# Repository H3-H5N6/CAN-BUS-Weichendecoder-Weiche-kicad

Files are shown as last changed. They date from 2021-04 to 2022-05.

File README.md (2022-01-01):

# CAN-BUS Weichendecoder

## Serielle Console
Auf der seriellen Console kann man die Konfiguration einsehen und und die Modul-Id ändern.

Die Serielle Schnittstelle muss dazu auf 115200 gesetzt werden

## Konfigiratuion ansehen

Mit der Taste "p" wird die aktuelle Konfiguartion angezeigt. Beispiel:

```
==== CAN-Konfiguration ====
Version:       1
Status ID:     2
CAN ID: [0] => 811
CAN ID: [1] => 812
CAN ID: [2] => 813
CAN ID: [3] => 814
CAN ID: [4] => 815
CAN ID: [5] => 816
CAN ID: [6] => 817
CAN ID: [7] => 818
CAN ID: [8] => 819
CAN ID: [9] => 820
===========================
```

## Modul-Adresse ändern:

Mit der Eingabe &lt;i> + Nr + &lt;Return> kann die Modul-Adresse geändert werden.

```
Neue ID: 2
Setze neue Id: 2
```

Der Weichendecoder liefert regelmäßig seinen aktuellen Zustand

## Protocol

### IDs

* 100 Frames mit der Id 100 dient dem Verändern des Zustandes
* 200 Sendet den aktuellen Zustand des Decoders, wenn die im ersten Datafeld (u_int16) angegebene Moduladresse mit der des Moduls übereinstimmt. Der Status selbst wird mit der Id 300 gesendet

## CAN-Bus-RJ45-Steckerbelegung

Quelle: https://www.opendcc.de/info/can/can_connector.html

    CAN Pinbelegung auf RJ45
    RJ45 	
    Pin	Signal	    Beschreibung
    1 	CAN_H       Dominant High
    2 	CAN_L    	Dominant Low
    3 	CAN_GND     Ground
    4 	Reserved    Upgrade Path  // DCC A
    5 	Reserved    Upgrade Path  // DCC B
    6 	CAN_SHLD    CAN Shield, Optional
    7 	CAN_GND     Ground
    8 	CAN_V+ 	    Power, Optional

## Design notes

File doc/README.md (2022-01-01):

# Aktueller Stand (26.11.2021)

Kernstück des Ganzen sind die Weichendecoder für motorische Antriebe mit Impulssteuerung. Zum Einsatz sollen die Antriebe MP6 von MTB kommen. Diese werden mit kurzen Impulse gesteuert, indem der jeweilige Schalteingang kurz gegen Masse gezogen werden. Die Antriebe selbst werden mit 12V DC betrieben und haben auch gleich die Herzstückpolaristaion an Bord.

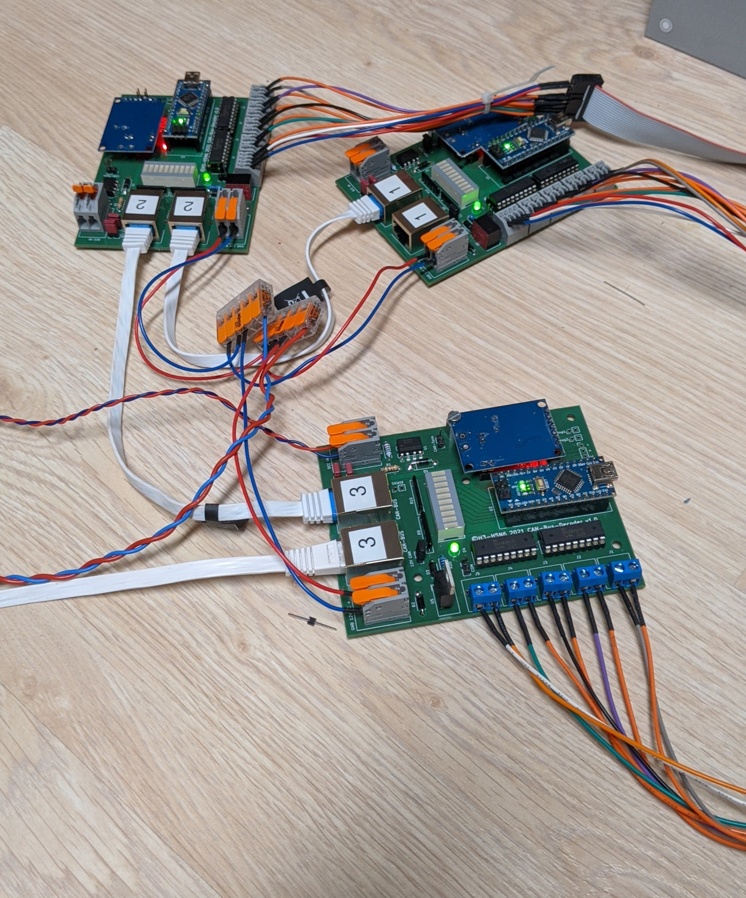
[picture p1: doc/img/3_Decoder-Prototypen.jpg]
Drei Weichendecoder


Geschaltet werden die Schaltausgänge 
* via CAN-BUS (und eigenem Protokoll)
* DCC
* oder für Testzwecke via USB-Console

CAN-BUS, DCC und auch 12V für die Versorgung der eigentlichen Elektronik erfolgt via einem RJ45-Netzwerkkabel.

Für Testzwecke gibt es auch eine kleine CAN-BUS-Zentrale  
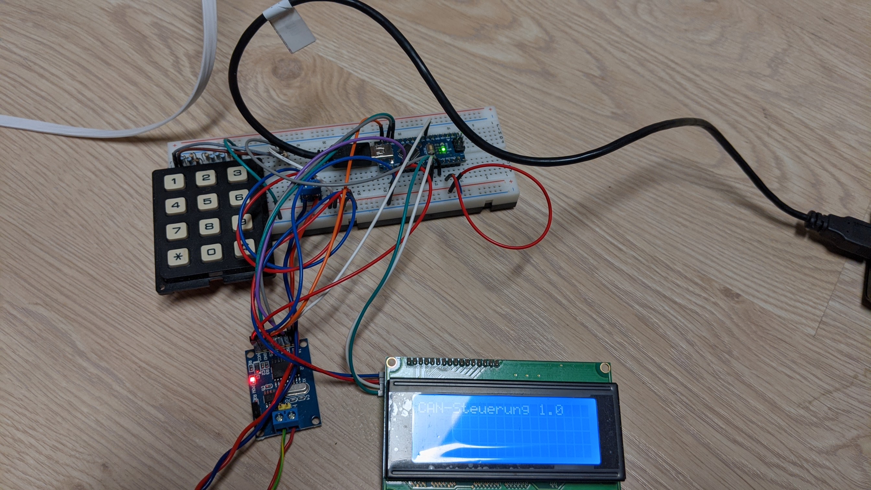
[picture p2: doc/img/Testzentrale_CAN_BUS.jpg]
CAN-Bus-Zentrale


Über die Eingabe von einer "Adresse" können die einzelnen Schaltausgänge geschaltet werden. Auch das Schalten von Weichenstraße ist möglich.

Später soll das Ganze durch ein Stellpult mit Schaltern (und LEDs zur Anzeige) ersetzt werden.

Natürlich kann man die Ausgänge auch mit einer gewöhnlichen DCC-Zentrale geschaltet werden. Hier als Beispiel kommt eine ECOS von ESU zu Einsatz, die auch ein Stellpult kennt.

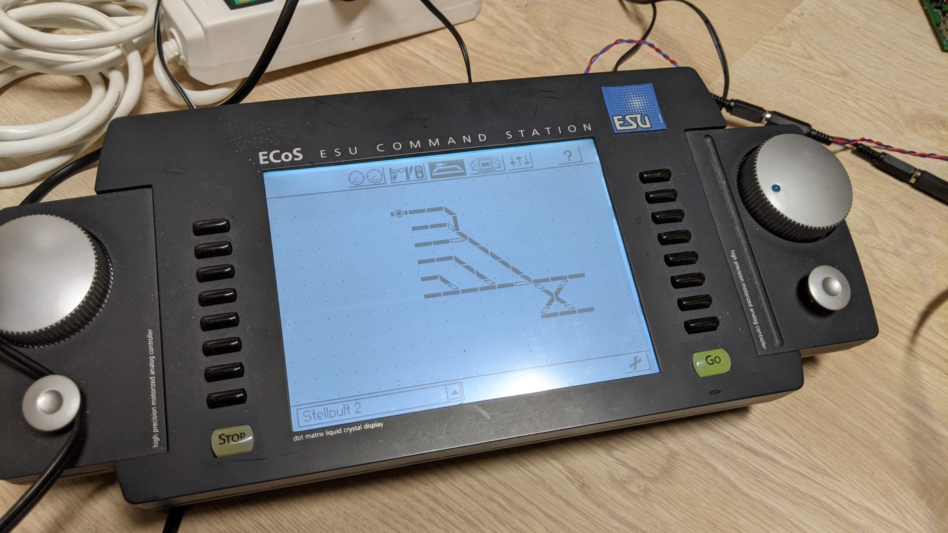
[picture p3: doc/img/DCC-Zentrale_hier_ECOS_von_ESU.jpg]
DCC-Zentrale


Da aktuell die Anlage ca 120km steht, wurde ein Modellbahn-Simulator gebaut. Die Weichenantriebe sind durch Bistabile Relais nachgebildet und die LED stellen die aktuelle Lage der Weichen wieder.

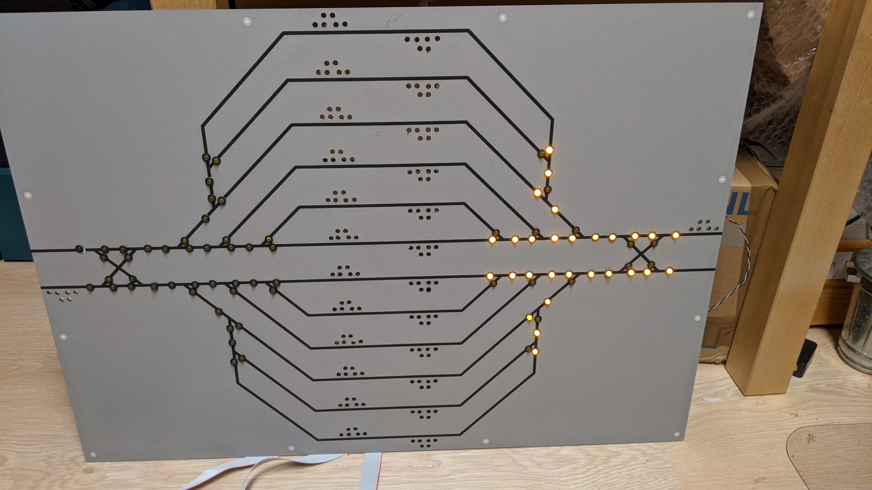
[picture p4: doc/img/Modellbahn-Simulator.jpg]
Modellbahn-Simulator

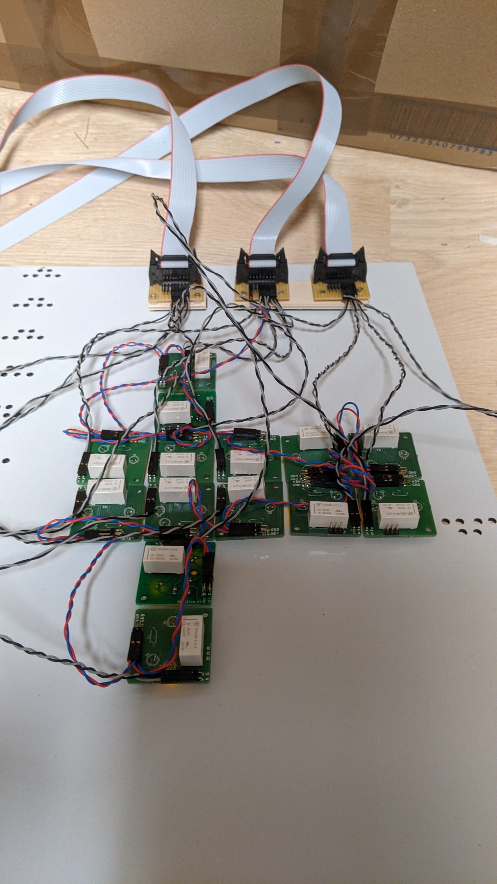
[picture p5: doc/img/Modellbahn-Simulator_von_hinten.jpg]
Modellbahn-Simulator Rückseite


# CAN-BUS-Frames

Die einzelnen Aktoren haben eine id im Wertebereich uint_16 (2byte)
## Aktor schalten

* Frame ID: 100
* data16: ID1 [, [ID2][, [ID3][, [ID4]]]]

Pro Frame können 4 Aktoren gleichzeit geschaltet werden

## Status der Aktoren

* Frame ID 300
* data16: ID des Aktor, Status des Aktors, unbenutz, ID des aktiven Aktors

### Bedeutung der Status

* OFF 0x00
* ON  0x01
* RUNNING 0x02
* BLOCKED_STATE 0x03
* UNKNOWN_STATE 0x04

Eine einfache Weiche besteht aus zwei Aktoren. Um den Status dieser Weiche zu erhalten, werden zwei Frames gesendet.

Hat der eine Aktor einen Status RUNNING, so hat der zweite Aktor einen Status von BLOCKED_STATE, da dieser aktuell nicht verändert werden kann. 

# Adapter Wannenstecker 2x3 zu Stiftleiste 1x6

## Adapter auf Lochrasterplatte, Ansicht von unten.


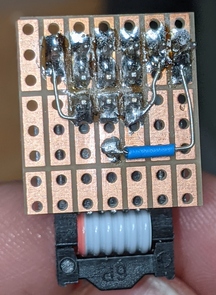
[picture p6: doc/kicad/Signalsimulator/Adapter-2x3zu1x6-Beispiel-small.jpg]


## Leiterplatte, Blick von oben auf die Bestückungsseite

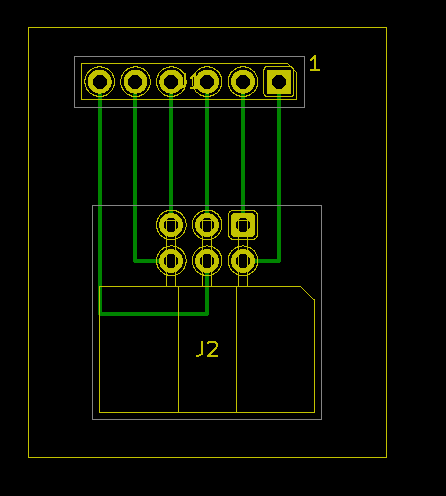
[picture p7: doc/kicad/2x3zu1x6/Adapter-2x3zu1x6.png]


## Belegung der 1x6-Stiftleiste, Blick von oben auf die Leiterplatte

6  |  5 |  4 |  3 | 2  | 1 
---|----|----|----|----|---
r1 | r2 | gr |  + | ge | w  

## Belegung des 2x3-Wannensteckers 

5  | 6  | 1  
---|----|----
r2 | r1 | w  
gr | +  | ge 
4  | 3  | 2

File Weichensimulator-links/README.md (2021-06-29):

# Weichensimulator links

## Releases
### v1.0

* Erster Entwurf

### v2.0

* Fix: Beschreibung der Platine auf der Oberseite, da Relais auf der Leiterseite plaziert wird 
* Change: 90°-Leiterbahnen durch 45° ersetzt

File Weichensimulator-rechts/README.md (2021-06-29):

# Weichensimulator rechts

## Releases
### v1.0

* Erster Entwurf, aber fehlerhaft: faĺsche Anordung der LEDs
### v2.0

* Fix: Anordnung der LEDs
* Change: Release auf Rückseite, damit die LEDs nur mit +3mm über Platine montiert werden müssen
* Change: Beschreibung auf der Vorderseite (da Relais nun auf der Rückseite); Beschreibzng auf Rückseite, da bei umgekehrter Bestückung das Teil für links verwendet werden kann.
* Change: Beschriftung für +5V und GND hinzugefügt (beide Seiten)
* Change: Pins des 2. Umschaltkontakts herausgeführt
* Chnage: Unterseite als Kupferfläche ausgeführt

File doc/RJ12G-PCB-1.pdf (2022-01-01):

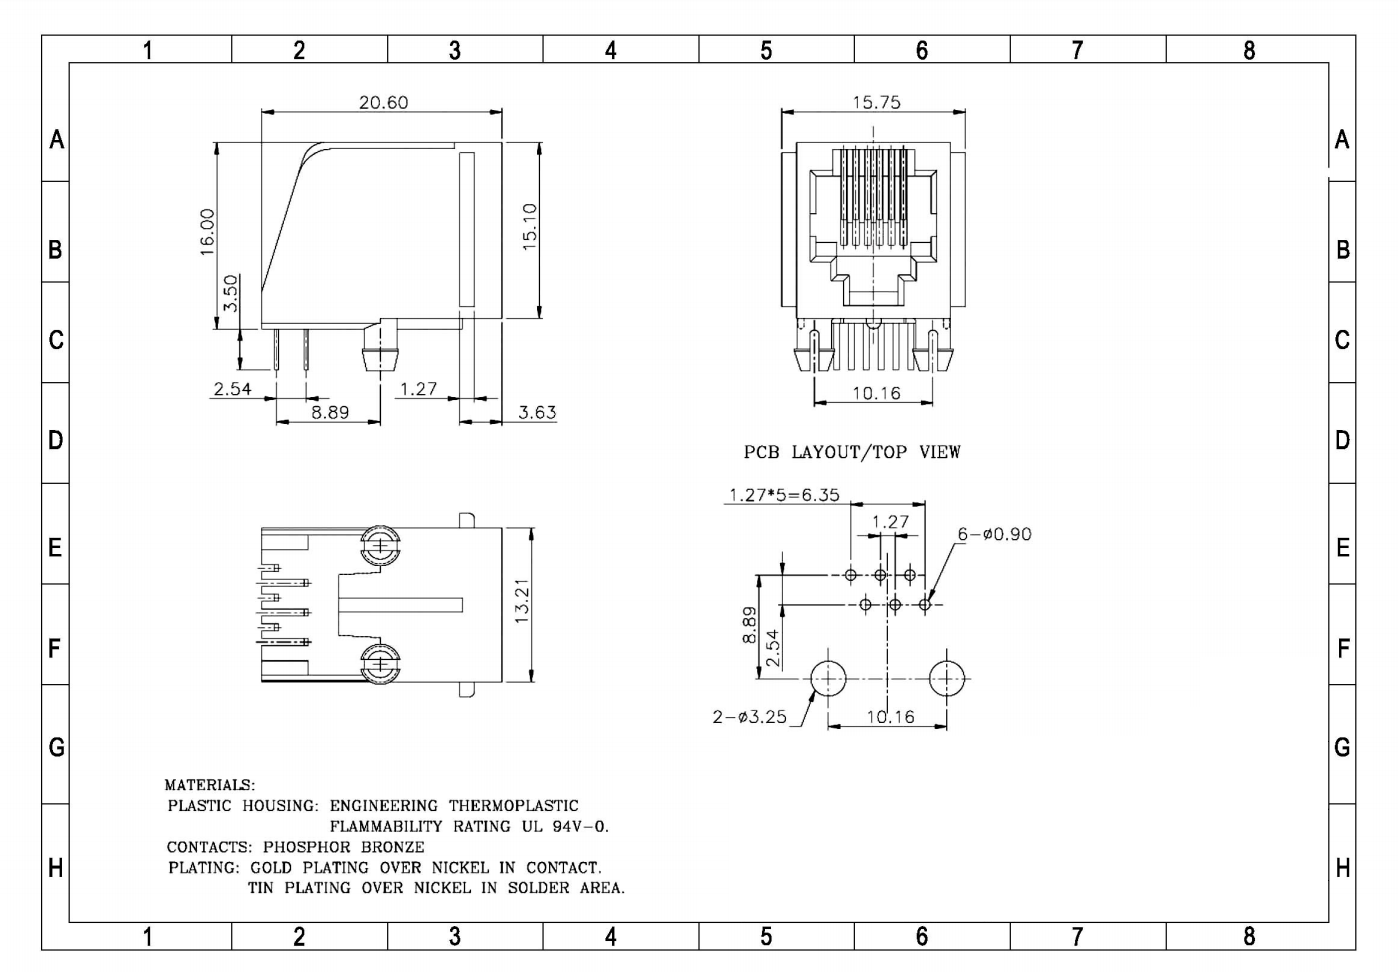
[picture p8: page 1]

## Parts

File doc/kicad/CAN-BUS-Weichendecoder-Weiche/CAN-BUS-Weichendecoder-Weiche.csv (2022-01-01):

Reference | Value | Footprint | Datasheet | Preis | Quelle | Description | Height | Manufacturer_Name | Manufacturer_Part_Number | Mouser Part Number | Mouser Price/Stock
Shield1 | CAN-BUS-MODULE | CAN-BUS-MODULE:MCP2515_CAN_MODULE |  | 2,90 | https://www.marotronics.de/MCP2515-Can-Bus-Modul-mit-TJA1050-Transciever-5V-SPI-Interface-fuer-Arduino-Pi
JP5 | Prog1 | Pin_Headers:Pin_Header_Straight_1x02_Pitch2.54mm | ~
JP6 | Prog2 | Pin_Headers:Pin_Header_Straight_1x02_Pitch2.54mm | ~
R6 | 10K | Resistors_THT:R_Axial_DIN0207_L6.3mm_D2.5mm_P7.62mm_Horizontal | ~
R5 | 22k | Resistors_THT:R_Axial_DIN0207_L6.3mm_D2.5mm_P7.62mm_Horizontal | ~
R4 | 4,7k | Resistors_THT:R_Axial_DIN0207_L6.3mm_D2.5mm_P7.62mm_Horizontal | ~
R8 | 4k7 | Resistors_THT:R_Axial_DIN0207_L6.3mm_D2.5mm_P7.62mm_Horizontal | ~
R7 | 4k7 | Resistors_THT:R_Axial_DIN0207_L6.3mm_D2.5mm_P7.62mm_Horizontal | ~
J23 | CAN-BUS | ASSMANN_WSW:A20042LPFS | ~ | 0,70 | https://www.reichelt.de/modular-einbaubuchse-8-8-geschirmt-mebp-8-8g-p24975.html?&nbc=1
U1 | 6N136 | Package_DIP:DIP-8_W7.62mm | https://optoelectronics.liteon.com/upload/download/DS70-2008-0032/6N135-L%206N136-L%20series.pdf | 0,52 | https://www.reichelt.de/optokoppler-6n-137-p2858.html
D1 | 1N4004 | Diodes_THT:D_DO-15_P10.16mm_Horizontal | http://www.vishay.com/docs/88503/1n4001.pdf
R1 | 1k5 | Resistors_THT:R_Axial_DIN0207_L6.3mm_D2.5mm_P7.62mm_Horizontal | ~
U2 | Arduino_Nano | Modules:Arduino_Nano | http://www.mouser.com/pdfdocs/Gravitech_Arduino_Nano3_0.pdf | 5,85 | https://www.makershop.de/plattformen/arduino/3-nano-v3/
R2 | 10K | Resistors_THT:R_Axial_DIN0207_L6.3mm_D2.5mm_P7.62mm_Horizontal | ~
J6 | GND 12V DC + | CONN_2604-1102_4_WAG
JP3 | CAN-Term | Pin_Headers:Pin_Header_Straight_1x02_Pitch2.54mm | ~
R10 | 1k | Resistors_THT:R_Array_SIP6 | http://www.vishay.com/docs/31509/csc.pdf
J5 | 250-1404 | Wago:CONN_250-1404_WAG
R9 | 1k | Resistors_THT:R_Array_SIP6 | http://www.vishay.com/docs/31509/csc.pdf
DS1 | DC-10SGWA | Kingbright-LED:DIPS750W80P254L2540H825Q20N | http://uk.rs-online.com/web/p/products/2473090 | 2,10 | https://www.reichelt.de/bargraph-anzeige-10-elemente-gruen-gbg-1000-p8141.html?&nbc=1 | Kingbright DC-10SGWA Light Bar LED Display, Green 21 mcd | 8.25 | Kingbright | DC-10SGWA | N/A | https://www.mouser.com/Search/Refine.aspx?Keyword=N%2FA
J4 | 250-1404 | Wago:CONN_250-1404_WAG
J3 | 250-1404 | Wago:CONN_250-1404_WAG
JP7 | COM | Pin_Headers:Pin_Header_Straight_1x02_Pitch2.54mm | ~
U3 | ULN2803A | Package_DIP:DIP-18_W7.62mm | http://www.ti.com/lit/ds/symlink/uln2803a.pdf | 0,41 | https://www.reichelt.de/eight-darlington-arrays-dil-18-uln-2803a-p22085.html?search=ULN2803A
J2 | 250-1404 | Wago:CONN_250-1404_WAG
J22 | CAN-BUS | ASSMANN_WSW:A20042LPFS | ~ | 0,70 | https://www.reichelt.de/modular-einbaubuchse-8-8-geschirmt-mebp-8-8g-p24975.html?&nbc=1
JP1 | DCC B | Pin_Headers:Pin_Header_Straight_1x02_Pitch2.54mm | ~
JP2 | DCC CAN | Pin_Headers:Pin_Header_Straight_1x02_Pitch2.54mm | ~
JP4 | 12V CAN | Pin_Headers:Pin_Header_Straight_1x02_Pitch2.54mm | ~
J7 | DCC IN | CONN_2604-1102_4_WAG
U5 | TSR_1-2450 | Converters_DCDC_ACDC:DCDC-Conv_TRACO_TSR-1 | http://www.tracopower.com/products/tsr1.pdf
D2 | 1N4001 | Diodes_THT:D_DO-41_SOD81_P7.62mm_Horizontal | ~
R20 | 470 | Resistors_THT:R_Axial_DIN0207_L6.3mm_D2.5mm_P7.62mm_Horizontal | ~
D4 | LED | LEDs:LED_D3.0mm | ~
H1 | MountingHole | Mounting_Holes:MountingHole_3.2mm_M3 | ~
H2 | MountingHole | Mounting_Holes:MountingHole_3.2mm_M3 | ~
H3 | MountingHole | Mounting_Holes:MountingHole_3.2mm_M3 | ~
H4 | MountingHole | Mounting_Holes:MountingHole_3.2mm_M3 | ~
J1 | 250-1404 | Wago:CONN_250-1404_WAG
D3 | 1N4001 | Diodes_THT:D_DO-41_SOD81_P7.62mm_Horizontal | ~
J8 | I²C D C + - | Pin_Headers:Pin_Header_Straight_1x04_Pitch2.54mm | ~
JP8 | Shield | Pin_Headers:Pin_Header_Straight_1x02_Pitch2.54mm | ~
U4 | ULN2803A | Package_DIP:DIP-18_W7.62mm | http://www.ti.com/lit/ds/symlink/uln2803a.pdf | 0,41 | https://www.reichelt.de/eight-darlington-arrays-dil-18-uln-2803a-p22085.html?search=ULN2803A

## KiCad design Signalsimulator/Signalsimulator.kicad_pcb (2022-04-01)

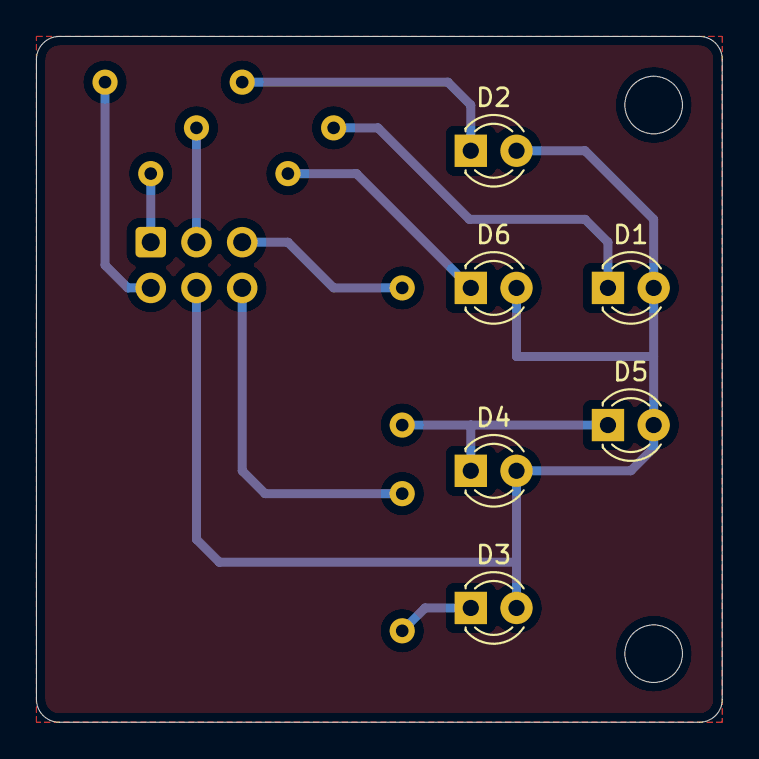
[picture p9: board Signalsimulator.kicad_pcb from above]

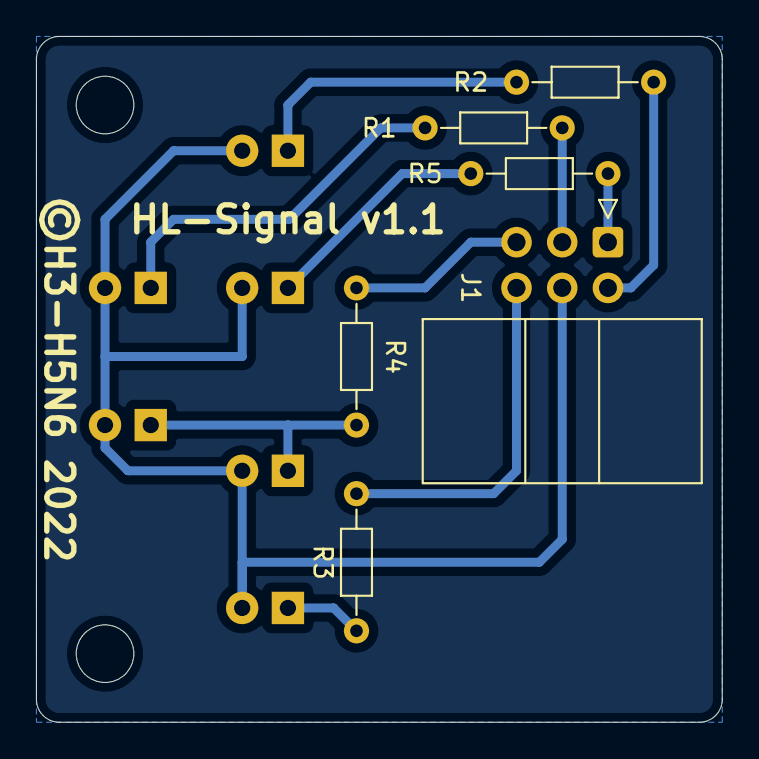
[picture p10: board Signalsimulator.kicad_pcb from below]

Board: 2 copper layers, 38.1 x 38.1 mm, 14 parts (6 on the bottom side), 11 nets.

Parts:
D1: Rot 2; LED_D3.0mm
D2: Grün; LED_D3.0mm
D3: Gelb; LED_D3.0mm
D4, D5: Weiß; LED_D3.0mm
D6: Rot 1; LED_D3.0mm
H1, H1#2: MountingHole; MountingHole_3.2mm_M3
J1: Conn_02x03_Odd_Even; IDC-Header_2x03_P2.54mm_Horizontal
R1, R2, R3, R4, R5: R; R_Axial_DIN0204_L3.6mm_D1.6mm_P7.62mm_Horizontal

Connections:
+5P: D1.2, D2.2, D3.2, D4.2, D5.2, D6.2, J1.4
unnamed: D1.1, R1.1
unnamed: D2.1, R2.1
unnamed: D3.1, R3.1
unnamed: D4.1, D5.1, R4.1
unnamed: D6.1, R5.1
unnamed: J1.1, R5.2
unnamed: J1.2, R2.2
unnamed: J1.3, R1.2
unnamed: J1.5, R4.2
unnamed: J1.6, R3.2

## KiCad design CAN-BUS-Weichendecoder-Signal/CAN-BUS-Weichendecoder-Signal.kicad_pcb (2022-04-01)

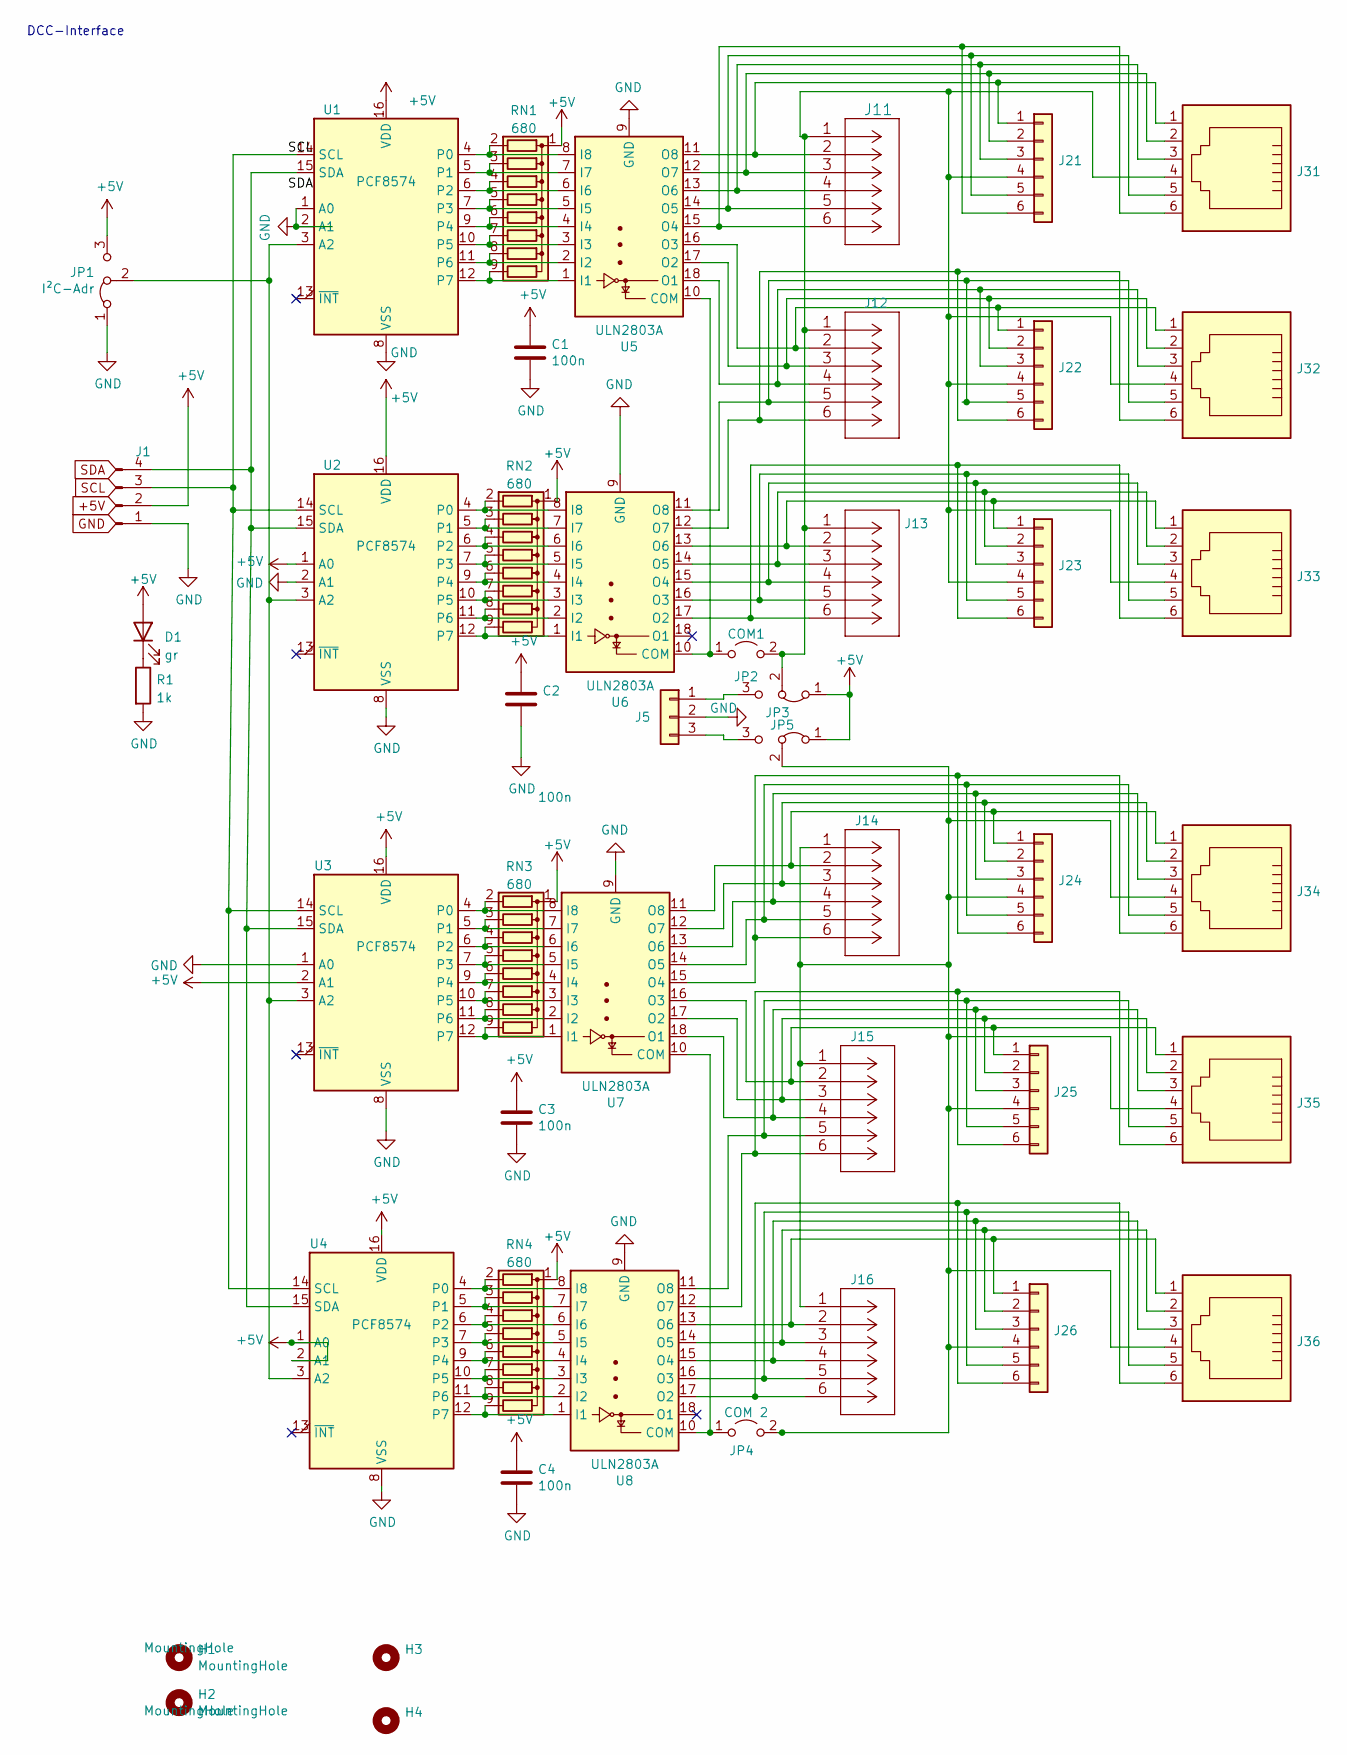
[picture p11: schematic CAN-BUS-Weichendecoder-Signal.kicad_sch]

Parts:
C1, C2, C3, C4: 100n; C_Disc_D7.0mm_W2.5mm_P5.00mm
D1: gr; LED_D3.0mm
H1, H2, H3, H4: MountingHole; MountingHole_3.2mm_M3
J1: Conn_01x04_Male; Pin_Header_Straight_1x04_Pitch2.54mm
J5: Conn_01x03; TerminalBlock_bornier-3_P5.08mm
J11: 250-1406; CONN_250-1406_WAG_Light
J12, J13, J14, J15, J16: Wago 250-1406; CONN_250-1406_WAG_Light
J21, J22, J23, J24, J25, J26: Conn_01x06; IDC-Header_2x03_P2.54mm_Vertical_Light
J31, J32, J33, J34, J35, J36: RJ12; RJ12_Amphenol_54601_Light
JP1: I²C-Adr; Pin_Header_Straight_1x03_Pitch2.54mm
JP2: COM1; PinHeader_1x02_P2.54mm_Vertical
JP3, JP5: Jumper_3_Bridged12; PinHeader_1x03_P2.54mm_Vertical
JP4: COM 2; PinHeader_1x02_P2.54mm_Vertical
R1: 1k; R_Axial_DIN0207_L6.3mm_D2.5mm_P7.62mm_Horizontal
RN1, RN2, RN3, RN4: 680; R_Array_SIP9
U1, U2, U3, U4: PCF8574; DIP-16_W7.62mm
U5, U6, U7, U8: ULN2803A; DIP-18_W7.62mm

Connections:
+5V: C1.1, C2.1, C3.1, C4.1, D1.2 (A), J1.2, JP1.3 (B), JP3.1 (A), JP5.1 (A), RN1.1 (common), RN2.1 (common), RN3.1 (common), RN4.1 (common), U1.16 (VDD), U2.1 (A0), U2.16 (VDD), U3.2 (A1), U3.16 (VDD), U4.1 (A0), U4.2 (A1), U4.16 (VDD)
GND: C1.2, C2.2, C3.2, C4.2, J1.1, J5.2, JP1.1 (A), R1.2, U1.1 (A0), U1.2 (A1), U1.8 (VSS), U2.2 (A1), U2.8 (VSS), U3.1 (A0), U3.8 (VSS), U4.8 (VSS), U5.9 (GND), U6.9 (GND), U7.9 (GND), U8.9 (GND)
unnamed: J1.4, U1.15 (SDA), U2.15 (SDA), U3.15 (SDA), U4.15 (SDA)
unnamed: J5.1, JP3.3 (B)
unnamed: J5.3, JP5.3 (B)
unnamed: J11.1, J12.1, J13.1, J21.4, J22.4, J23.4, J31.4, J32.4, J33.4, JP2.2 (B), JP3.2 (C)
unnamed: J11.2, J21.1, J31.1, U5.11 (O8)
unnamed: J11.3, J21.2, J31.2, U5.12 (O7)
unnamed: J11.4, J21.3, J31.3, U5.13 (O6)
unnamed: J11.5, J21.5, J31.5, U5.14 (O5)
unnamed: J11.6, J21.6, J31.6, U5.15 (O4)
unnamed: J12.2, J22.1, J32.1, U5.16 (O3)
unnamed: J12.3, J22.2, J32.2, U5.17 (O2)
unnamed: J12.4, J22.3, J32.3, U5.18 (O1)
unnamed: J12.5, J22.5, J32.5, U6.11 (O8)
unnamed: J12.6, J22.6, J32.6, U6.12 (O7)
unnamed: J13.2, J23.1, J33.1, U6.13 (O6)
unnamed: J13.3, J23.2, J33.2, U6.14 (O5)
unnamed: J13.4, J23.3, J33.3, U6.15 (O4)
unnamed: J13.5, J23.5, J33.5, U6.16 (O3)
unnamed: J13.6, J23.6, J33.6, U6.17 (O2)
unnamed: J14.1, J15.1, J16.1, J24.4, J25.4, J26.4, J34.4, J35.4, J36.4, JP4.2 (B), JP5.2 (C)
unnamed: J14.2, J24.1, J34.1, U7.11 (O8)
unnamed: J14.3, J24.2, J34.2, U7.12 (O7)
unnamed: J14.4, J24.3, J34.3, U7.13 (O6)
unnamed: J14.5, J24.5, J34.5, U7.14 (O5)
unnamed: J14.6, J24.6, J34.6, U7.15 (O4)
unnamed: J15.2, J25.1, J35.1, U7.16 (O3)
unnamed: J15.3, J25.2, J35.2, U7.17 (O2)
unnamed: J15.4, J25.3, J35.3, U7.18 (O1)
unnamed: J15.5, J25.5, J35.5, U8.11 (O8)
unnamed: J15.6, J25.6, J35.6, U8.12 (O7)
unnamed: J16.2, J26.1, J36.1, U8.13 (O6)
unnamed: J16.3, J26.2, J36.2, U8.14 (O5)
unnamed: J16.4, J26.3, J36.3, U8.15 (O4)
unnamed: J16.5, J26.5, J36.5, U8.16 (O3)
unnamed: J16.6, J26.6, J36.6, U8.17 (O2)
unnamed: JP1.2 (C), U1.3 (A2), U2.3 (A2), U3.3 (A2), U4.3 (A2)
unnamed: JP2.1 (A), U5.10 (COM), U6.10 (COM)
unnamed: JP4.1 (A), U7.10 (COM), U8.10 (COM)
unnamed: D1.1 (K), R1.1
unnamed: RN1.2 (R1), U1.4 (P0), U5.8 (I8)
unnamed: RN1.3 (R2), U1.5 (P1), U5.7 (I7)
unnamed: RN1.4 (R3), U1.6 (P2), U5.6 (I6)
unnamed: RN1.5 (R4), U1.7 (P3), U5.5 (I5)
unnamed: RN1.6 (R5), U1.9 (P4), U5.4 (I4)
unnamed: RN1.7 (R6), U1.10 (P5), U5.3 (I3)
unnamed: RN1.8 (R7), U1.11 (P6), U5.2 (I2)
unnamed: RN1.9 (R8), U1.12 (P7), U5.1 (I1)
unnamed: RN2.2 (R1), U2.4 (P0), U6.8 (I8)
unnamed: RN2.3 (R2), U2.5 (P1), U6.7 (I7)
unnamed: RN2.4 (R3), U2.6 (P2), U6.6 (I6)
unnamed: RN2.5 (R4), U2.7 (P3), U6.5 (I5)
unnamed: RN2.6 (R5), U2.9 (P4), U6.4 (I4)
unnamed: RN2.7 (R6), U2.10 (P5), U6.3 (I3)
unnamed: RN2.8 (R7), U2.11 (P6), U6.2 (I2)
unnamed: RN2.9 (R8), U2.12 (P7), U6.1 (I1)
unnamed: RN3.2 (R1), U3.4 (P0), U7.8 (I8)
unnamed: RN3.3 (R2), U3.5 (P1), U7.7 (I7)
unnamed: RN3.4 (R3), U3.6 (P2), U7.6 (I6)
unnamed: RN3.5 (R4), U3.7 (P3), U7.5 (I5)
unnamed: RN3.6 (R5), U3.9 (P4), U7.4 (I4)
unnamed: RN3.7 (R6), U3.10 (P5), U7.3 (I3)
unnamed: RN3.8 (R7), U3.11 (P6), U7.2 (I2)
unnamed: RN3.9 (R8), U3.12 (P7), U7.1 (I1)
unnamed: RN4.2 (R1), U4.4 (P0), U8.8 (I8)
unnamed: RN4.3 (R2), U4.5 (P1), U8.7 (I7)
unnamed: RN4.4 (R3), U4.6 (P2), U8.6 (I6)
unnamed: RN4.5 (R4), U4.7 (P3), U8.5 (I5)
unnamed: RN4.6 (R5), U4.9 (P4), U8.4 (I4)
unnamed: RN4.7 (R6), U4.10 (P5), U8.3 (I3)
unnamed: RN4.8 (R7), U4.11 (P6), U8.2 (I2)
unnamed: RN4.9 (R8), U4.12 (P7), U8.1 (I1)
SCL: J1.3, U1.14 (SCL), U2.14 (SCL), U3.14 (SCL), U4.14 (SCL)

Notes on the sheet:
DCC-Interface

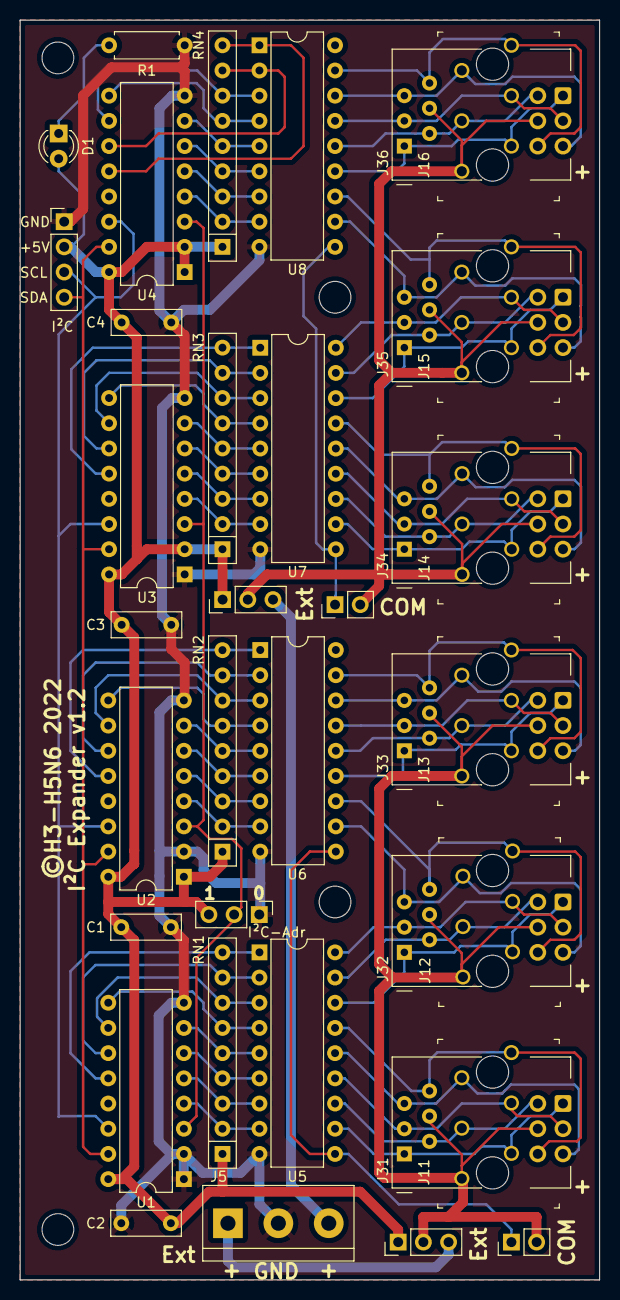
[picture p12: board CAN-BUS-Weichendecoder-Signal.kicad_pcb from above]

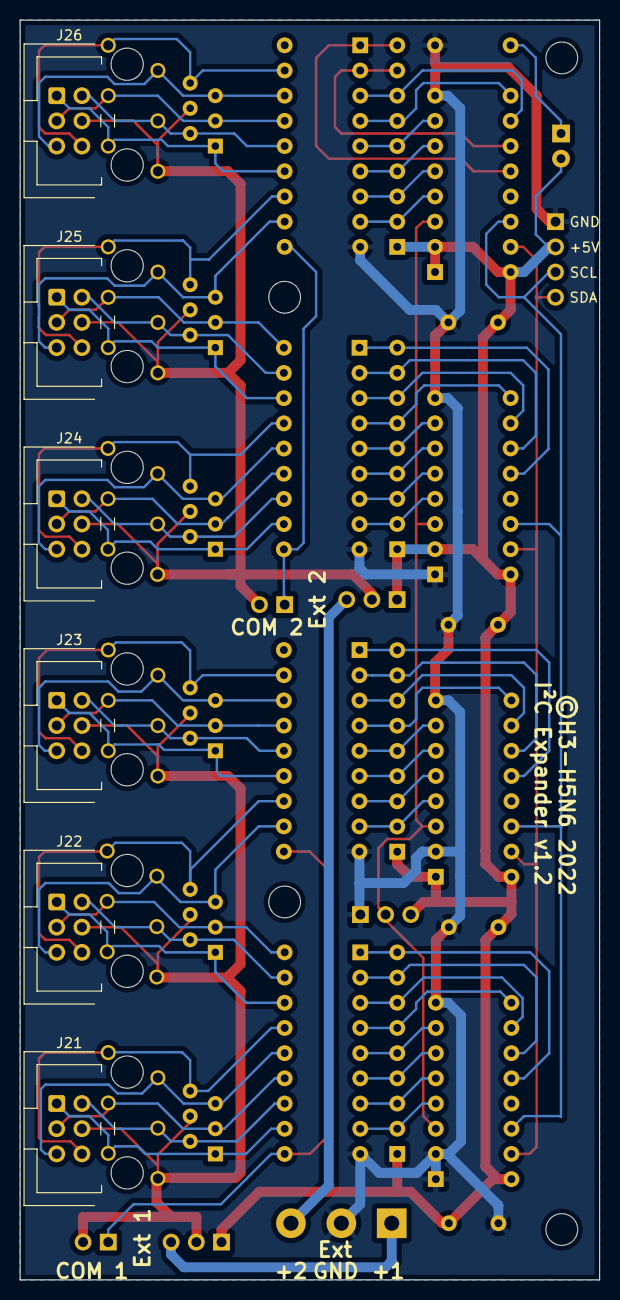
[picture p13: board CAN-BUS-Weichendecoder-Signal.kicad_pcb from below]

Board: 2 copper layers, 58.4 x 127.0 mm, 47 parts (6 on the bottom side), 74 nets.

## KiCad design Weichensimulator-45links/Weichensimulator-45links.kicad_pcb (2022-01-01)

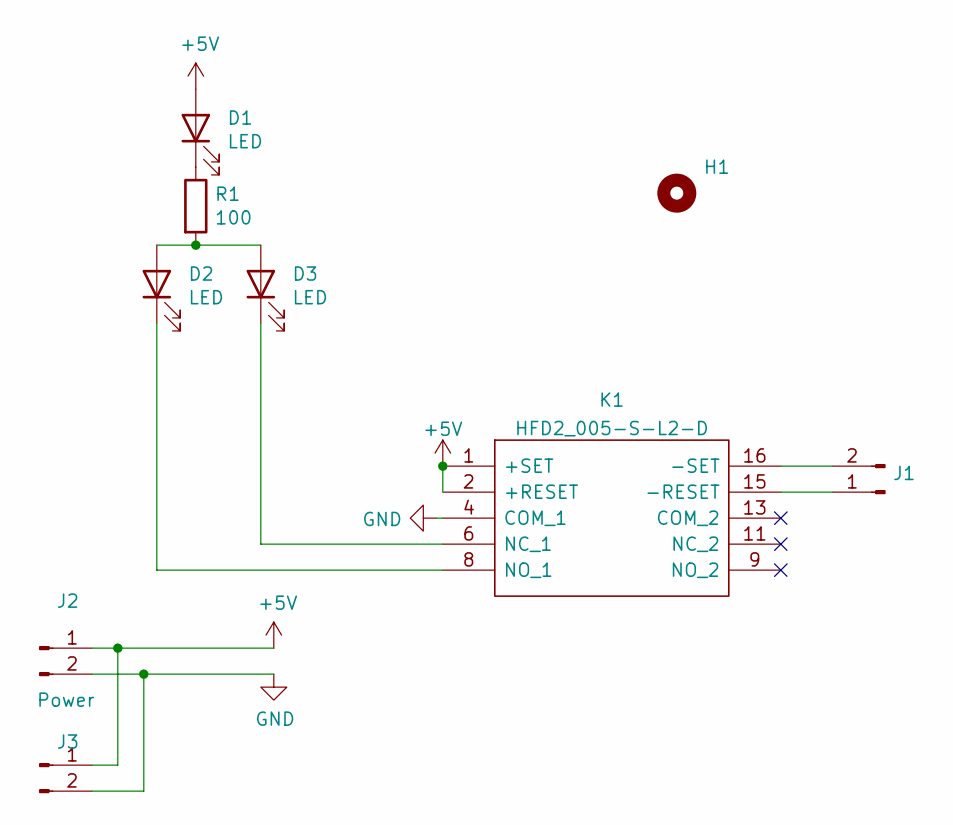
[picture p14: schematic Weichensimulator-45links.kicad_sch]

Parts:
D1, D2, D3: LED; LED_D5.0mm
H1: MountingHole; MountingHole_3.2mm_M3
J1, J3: Conn_01x02_Male; Pin_Header_Angled_1x02_Pitch2.54mm
J2: Power; Pin_Header_Angled_1x02_Pitch2.54mm
K1: HFD2_005-S-L2-D; HFD2005SL2D; Manufacturer_Part_Number HFD2/005-S-L2-D
R1: 100; R_Axial_DIN0207_L6.3mm_D2.5mm_P7.62mm_Horizontal

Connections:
+5V: D1.2 (A), J2.1, J3.1, K1.1 (+SET), K1.2 (+RESET)
GND: J2.2, J3.2, K1.4 (COM_1)
unnamed: D1.1 (K), R1.1
unnamed: D2.1 (K), K1.8 (NO_1)
unnamed: D2.2 (A), D3.2 (A), R1.2
unnamed: D3.1 (K), K1.6 (NC_1)
unnamed: J1.1, K1.15 (-RESET)
unnamed: J1.2, K1.16 (-SET)

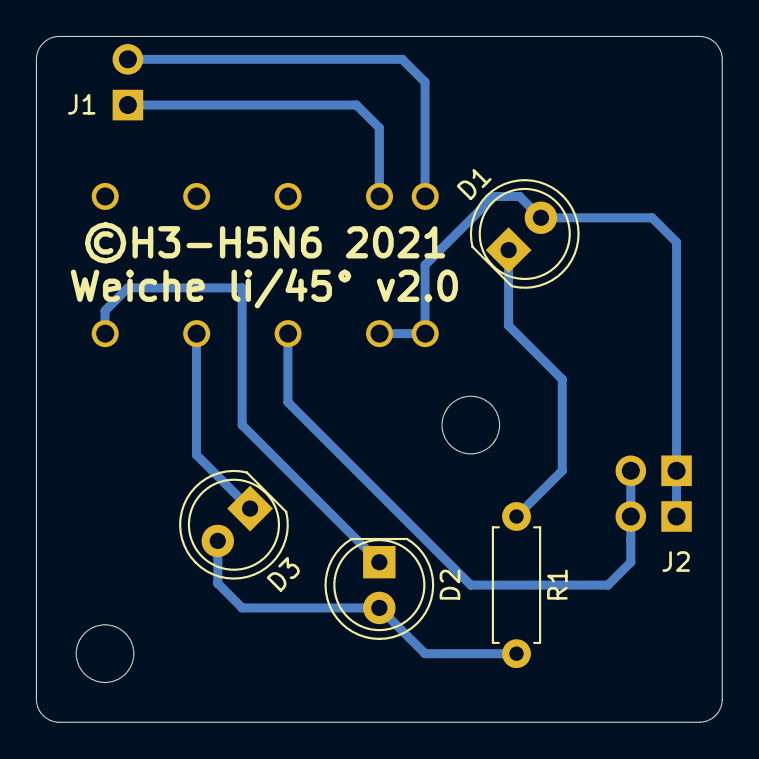
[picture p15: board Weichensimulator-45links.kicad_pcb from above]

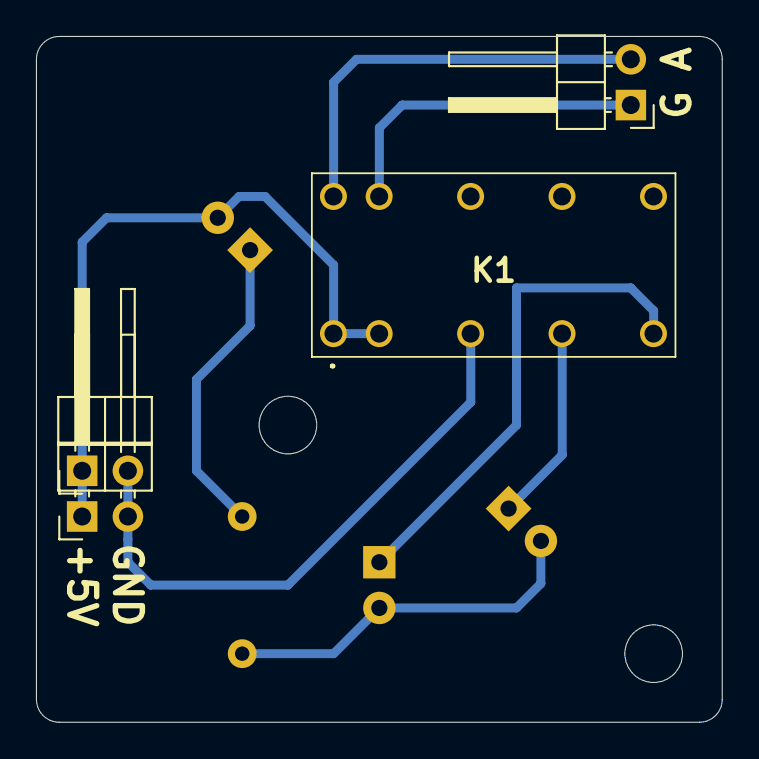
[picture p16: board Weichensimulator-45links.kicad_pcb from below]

Board: 2 copper layers, 38.1 x 38.1 mm, 10 parts (4 on the bottom side), 8 nets.

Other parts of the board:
H1#2: MountingHole; MountingHole_3.2mm_M3

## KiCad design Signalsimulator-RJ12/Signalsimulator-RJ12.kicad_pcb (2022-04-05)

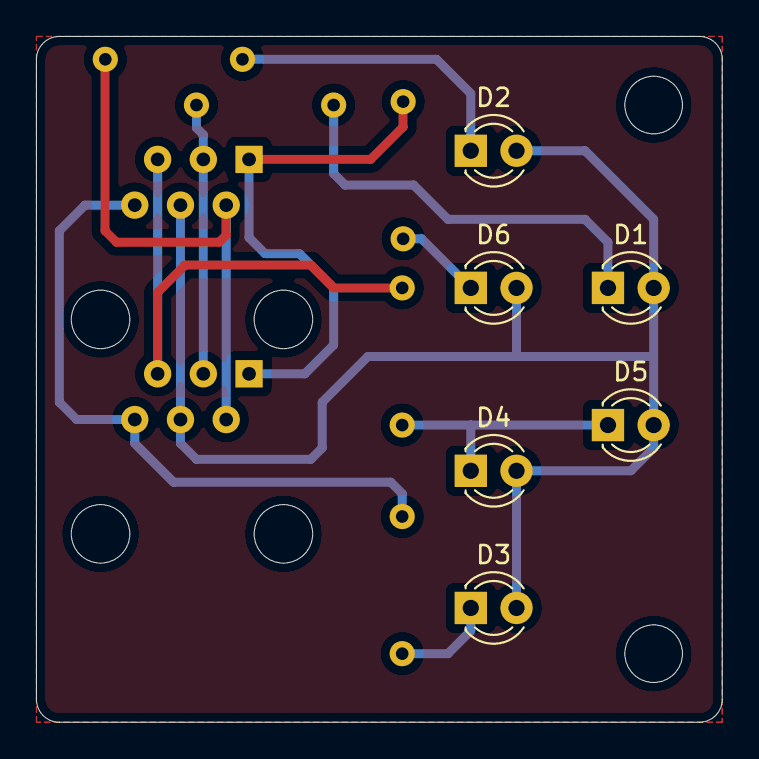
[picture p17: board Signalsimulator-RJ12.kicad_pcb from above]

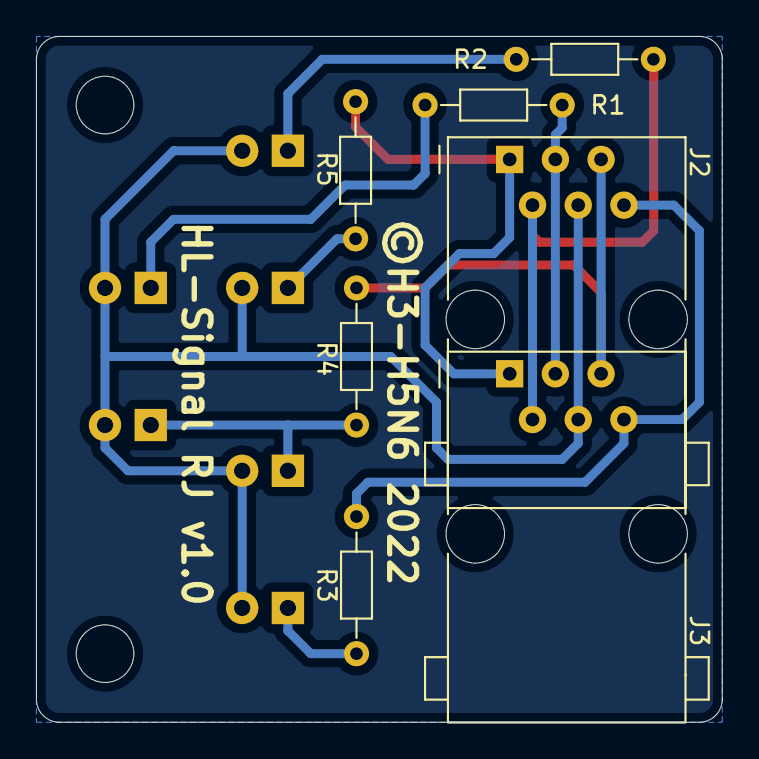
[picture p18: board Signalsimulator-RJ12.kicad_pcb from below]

Board: 2 copper layers, 38.1 x 38.1 mm, 15 parts (7 on the bottom side), 11 nets.

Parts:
3k3: R3; R_Axial_DIN0204_L3.6mm_D1.6mm_P7.62mm_Horizontal
D1: Rot 2; LED_D3.0mm
D2: Grün; LED_D3.0mm
D3: Gelb; LED_D3.0mm
D4, D5: Weiß; LED_D3.0mm
D6: Rot 1; LED_D3.0mm
H1, H1#2: MountingHole; MountingHole_3.2mm_M3
J2, J3: RJ12; RJ12_ECON
R1, R2, R5: 3k3; R_Axial_DIN0204_L3.6mm_D1.6mm_P7.62mm_Horizontal
R4: 2k2; R_Axial_DIN0204_L3.6mm_D1.6mm_P7.62mm_Horizontal

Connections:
+5P: D1.2 (A), D2.2 (A), D3.2 (A), D4.2 (A), D5.2 (A), D6.2 (A), J2.4, J3.4
unnamed: 3k3.1, D3.1 (K)
unnamed: 3k3.2, J2.6, J3.6
unnamed: D1.1 (K), R1.1
unnamed: D2.1 (K), R2.1
unnamed: D4.1 (K), D5.1 (K), R4.1
unnamed: D6.1 (K), R5.1
unnamed: J2.1, J3.1, R5.2
unnamed: J2.2, J3.2, R2.2
unnamed: J2.3, J3.3, R1.2
unnamed: J2.5, J3.5, R4.2

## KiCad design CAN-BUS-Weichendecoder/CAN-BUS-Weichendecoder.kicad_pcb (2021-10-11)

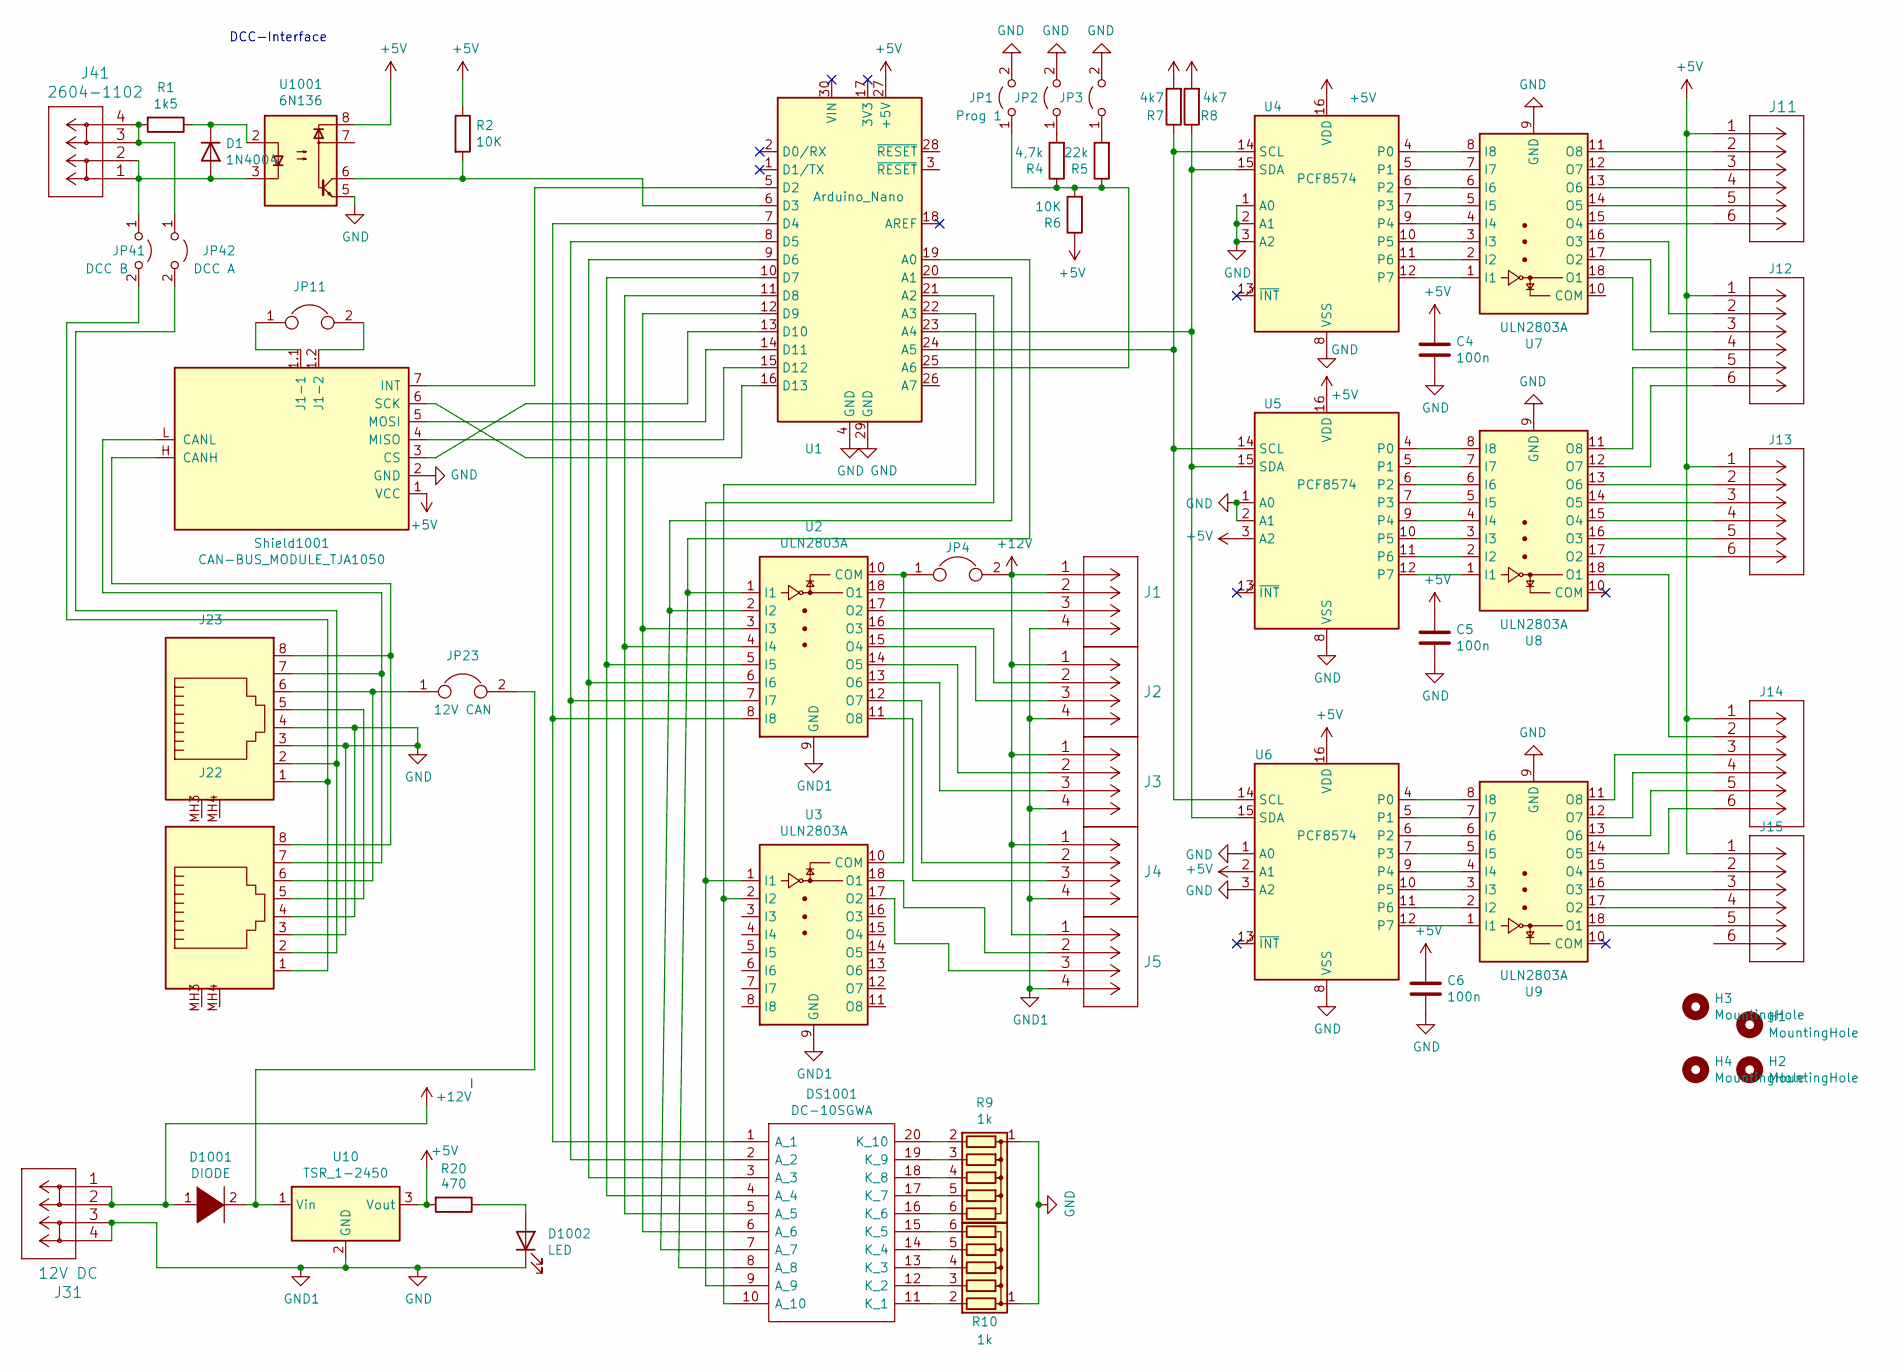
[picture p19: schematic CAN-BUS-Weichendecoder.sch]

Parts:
C4, C5, C6: 100n; C_Disc_D7.0mm_W2.5mm_P5.00mm
D1: 1N4004; D_DO-15_P10.16mm_Horizontal
D1001: DIODE; D_DO-15_P10.16mm_Horizontal
D1002: LED; LED_D3.0mm
DS1001: DC-10SGWA; DIPS750W80P254L2540H825Q20N; Manufacturer_Part_Number DC-10SGWA; Mouser Part Number N/A
H1, H2, H3, H4: MountingHole; MountingHole_3.2mm_M3
J1, J2, J3, J4, J5: 250-1404
J11: 250-1406; CONN_250-1406_WAG
J12, J13, J14, J15: Wago 250-1406; CONN_250-1406_WAG
J22, J23: J22; A20042LPFS
J31: 12V DC; CONN_2604-1102_4_WAG
J41: 2604-1102; CONN_2604-1102_4_WAG
JP1: Prog 1; Pin_Header_Straight_1x02_Pitch2.54mm
JP2: Prog2; Pin_Header_Straight_1x02_Pitch2.54mm
JP3: Prog3; Pin_Header_Straight_1x02_Pitch2.54mm
JP4, JP11: Jumper; Pin_Header_Straight_1x02_Pitch2.54mm
JP23: 12V CAN; Pin_Header_Straight_1x02_Pitch2.54mm
JP41: DCC B; Pin_Header_Straight_1x02_Pitch2.54mm
JP42: DCC A; Pin_Header_Straight_1x02_Pitch2.54mm
R1: 1k5; R_Axial_DIN0207_L6.3mm_D2.5mm_P7.62mm_Horizontal
R2, R6: 10K; R_Axial_DIN0207_L6.3mm_D2.5mm_P7.62mm_Horizontal
R4: 4,7k; R_Axial_DIN0207_L6.3mm_D2.5mm_P7.62mm_Horizontal
R5: 22k; R_Axial_DIN0207_L6.3mm_D2.5mm_P7.62mm_Horizontal
R7, R8: 4k7; R_Axial_DIN0207_L6.3mm_D2.5mm_P7.62mm_Horizontal
R9, R10: 1k; R_Array_SIP6
R20: 470; R_Axial_DIN0207_L6.3mm_D2.5mm_P7.62mm_Horizontal
Shield1001: CAN-BUS_MODULE_TJA1050; MCP2515_CAN_MODULE_BY0-10
U1: Arduino_Nano
U2, U3, U7, U8, U9: ULN2803A; DIP-18_W7.62mm
U4, U5, U6: PCF8574; DIP-16_W7.62mm
U10: TSR_1-2450; DCDC-Conv_TRACO_TSR-1
U1001: 6N136; DIP-8_W7.62mm

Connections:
+5V: C4.1, C5.1, C6.1, J11.1, J12.1, J13.1, J14.1, J15.1, R2.1, R6.1, R7.2, R8.2, R20.2, Shield1001.1 (VCC), U1.27 (+5V), U4.16 (VDD), U5.3 (A2), U5.16 (VDD), U6.2 (A1), U6.16 (VDD), U10.3 (Vout), U1001.8
+12V: D1001.1 (K), J1.1, J2.1, J3.1, J4.1, J5.1, J31.1, J31.2, JP4.2
GND: C4.2, C5.2, C6.2, D1002.1 (K), J1.4, J2.4, J3.4, J4.4, J5.4, J22.3, J22.4, J23.3, J23.4, J31.3, J31.4, JP1.2 (B), JP2.2 (B), JP3.2 (B), R9.1 (common), R10.1 (common), Shield1001.2 (GND), U1.4 (GND), U1.29 (GND), U2.9 (GND), U3.9 (GND), U4.1 (A0), U4.2 (A1), U4.3 (A2), U4.8 (VSS), U5.1 (A0), U5.2 (A1), U5.8 (VSS), U6.1 (A0), U6.3 (A2), U6.8 (VSS), U7.9 (GND), U8.9 (GND), U9.9 (GND), U10.2 (GND), U1001.5
unnamed: D1.1 (K), R1.1, U1001.2
unnamed: D1.2 (A), J41.1, J41.2, JP41.1 (A), U1001.3
unnamed: D1001.2 (A), JP23.2, U10.1 (Vin)
unnamed: D1002.2 (A), R20.1
unnamed: DS1001.1 (A_1), U1.7 (D4), U2.8 (I8)
unnamed: DS1001.2 (A_2), U1.8 (D5), U2.7 (I7)
unnamed: DS1001.3 (A_3), U1.9 (D6), U2.6 (I6)
unnamed: DS1001.4 (A_4), U1.10 (D7), U2.5 (I5)
unnamed: DS1001.5 (A_5), U1.11 (D8), U2.4 (I4)
unnamed: DS1001.6 (A_6), U1.12 (D9), U2.3 (I3)
unnamed: DS1001.7 (A_7), U1.20 (A1), U2.2 (I2)
unnamed: DS1001.8 (A_8), U1.19 (A0), U2.1 (I1)
unnamed: DS1001.9 (A_9), U1.21 (A2), U3.1 (I1)
unnamed: DS1001.10 (A_10), U1.22 (A3), U3.2 (I2)
unnamed: DS1001.11 (K_1), R10.2 (R1)
unnamed: DS1001.12 (K_2), R10.3 (R2)
unnamed: DS1001.13 (K_3), R10.4 (R3)
unnamed: DS1001.14 (K_4), R10.5 (R4)
unnamed: DS1001.15 (K_5), R10.6 (R5)
unnamed: DS1001.16 (K_6), R9.6 (R5)
unnamed: DS1001.17 (K_7), R9.5 (R4)
unnamed: DS1001.18 (K_8), R9.4 (R3)
unnamed: DS1001.19 (K_9), R9.3 (R2)
unnamed: DS1001.20 (K_10), R9.2 (R1)
unnamed: J1.2, U2.18 (O1)
unnamed: J1.3, U2.17 (O2)
unnamed: J2.2, U2.16 (O3)
unnamed: J2.3, U2.15 (O4)
unnamed: J3.2, U2.14 (O5)
unnamed: J3.3, U2.13 (O6)
unnamed: J4.2, U2.12 (O7)
unnamed: J4.3, U2.11 (O8)
unnamed: J5.2, U3.18 (O1)
unnamed: J5.3, U3.17 (O2)
unnamed: J11.2, U7.11 (O8)
unnamed: J11.3, U7.12 (O7)
unnamed: J11.4, U7.13 (O6)
unnamed: J11.5, U7.14 (O5)
unnamed: J11.6, U7.15 (O4)
unnamed: J12.2, U7.16 (O3)
unnamed: J12.3, U7.17 (O2)
unnamed: J12.4, U7.18 (O1)
unnamed: J12.5, U8.11 (O8)
unnamed: J12.6, U8.12 (O7)
unnamed: J13.2, U8.13 (O6)
unnamed: J13.3, U8.14 (O5)
unnamed: J13.4, U8.15 (O4)
unnamed: J13.5, U8.16 (O3)
unnamed: J13.6, U8.17 (O2)
unnamed: J14.2, U8.18 (O1)
unnamed: J14.3, U9.11 (O8)
unnamed: J14.4, U9.12 (O7)
unnamed: J14.5, U9.13 (O6)
unnamed: J14.6, U9.14 (O5)
unnamed: J15.2, U9.15 (O4)
unnamed: J15.3, U9.16 (O3)
unnamed: J15.4, U9.17 (O2)
unnamed: J15.5, U9.18 (O1)
unnamed: J22.1, J23.1, JP41.2 (B)
unnamed: J22.2, J23.2, JP42.2 (B)
unnamed: J22.5, J23.5
unnamed: J22.6, J23.6, JP23.1
unnamed: J22.7, J23.7, Shield1001.L (CANL)
unnamed: J22.8, J23.8, Shield1001.H (CANH)
unnamed: J41.3, J41.4, JP42.1 (A), R1.2
unnamed: JP1.1 (A), R4.1, R5.1, R6.2, U1.25 (A6)
unnamed: JP2.1 (A), R4.2
unnamed: JP3.1 (A), R5.2
unnamed: JP4.1, U2.10 (COM), U3.10 (COM)
unnamed: JP11.1, Shield1001.1.1 (J1-1)
unnamed: JP11.2, Shield1001.1.2 (J1-2)
unnamed: R2.2, U1.6 (D3), U1001.6
unnamed: R7.1, U1.24 (A5), U4.14 (SCL), U5.14 (SCL), U6.14 (SCL)
unnamed: R8.1, U1.23 (A4), U4.15 (SDA), U5.15 (SDA), U6.15 (SDA)
unnamed: Shield1001.3 (CS), U1.13 (D10)
unnamed: Shield1001.4 (MISO), U1.15 (D12)
unnamed: Shield1001.5 (MOSI), U1.14 (D11)
unnamed: Shield1001.6 (SCK), U1.16 (D13)
unnamed: Shield1001.7 (INT), U1.5 (D2)
unnamed: U4.4 (P0), U7.8 (I8)
unnamed: U4.5 (P1), U7.7 (I7)
unnamed: U4.6 (P2), U7.6 (I6)
unnamed: U4.7 (P3), U7.5 (I5)
unnamed: U4.9 (P4), U7.4 (I4)
unnamed: U4.10 (P5), U7.3 (I3)
unnamed: U4.11 (P6), U7.2 (I2)
unnamed: U4.12 (P7), U7.1 (I1)
unnamed: U5.4 (P0), U8.8 (I8)
unnamed: U5.5 (P1), U8.7 (I7)
unnamed: U5.6 (P2), U8.6 (I6)
unnamed: U5.7 (P3), U8.5 (I5)
unnamed: U5.9 (P4), U8.4 (I4)
unnamed: U5.10 (P5), U8.3 (I3)
unnamed: U5.11 (P6), U8.2 (I2)
unnamed: U5.12 (P7), U8.1 (I1)
unnamed: U6.4 (P0), U9.8 (I8)
unnamed: U6.5 (P1), U9.7 (I7)
unnamed: U6.6 (P2), U9.6 (I6)
unnamed: U6.7 (P3), U9.5 (I5)
unnamed: U6.9 (P4), U9.4 (I4)
unnamed: U6.10 (P5), U9.3 (I3)
unnamed: U6.11 (P6), U9.2 (I2)
unnamed: U6.12 (P7), U9.1 (I1)

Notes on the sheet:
DCC-Interface

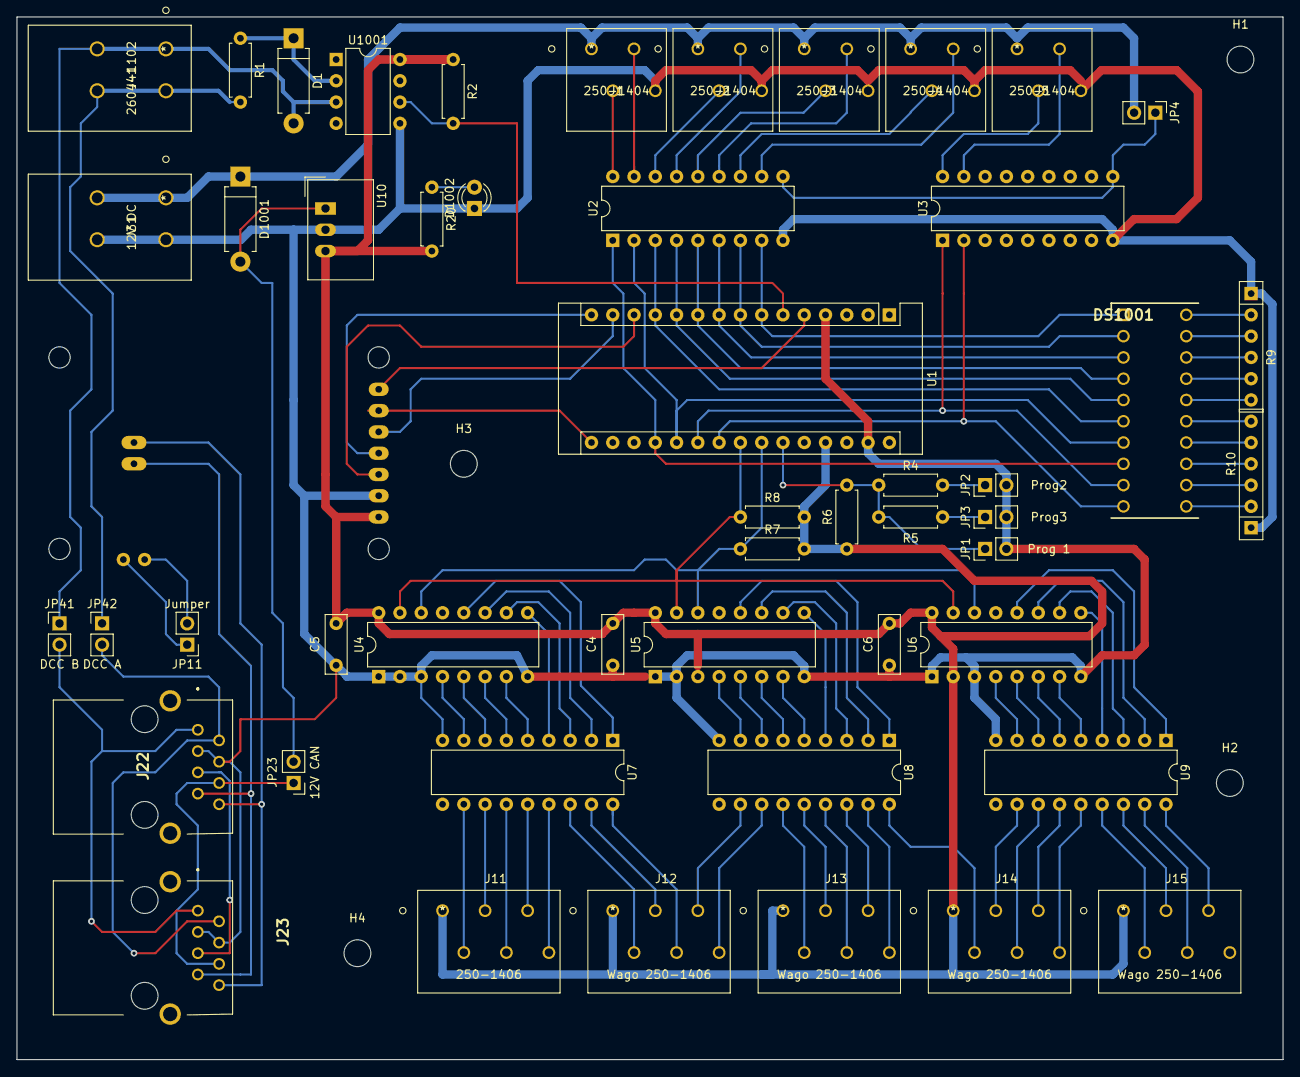
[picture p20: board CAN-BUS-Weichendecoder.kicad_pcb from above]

Board: 2 copper layers, 151.1 x 124.5 mm, 55 parts (1 on the bottom side), 106 nets.

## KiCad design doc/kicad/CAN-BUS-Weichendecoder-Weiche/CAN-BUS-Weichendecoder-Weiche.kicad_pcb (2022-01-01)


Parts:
C1: 22µ/16V; CP_Radial_D4.0mm_P1.50mm
D1: 1N4004; D_DO-15_P10.16mm_Horizontal
D2, D3: 1N4001; D_DO-41_SOD81_P7.62mm_Horizontal
D4: LED; LED_D3.0mm
DS1: DC-10SGWA; DIPS750W80P254L2540H825Q20N; Manufacturer_Part_Number DC-10SGWA; Mouser Part Number N/A
H1, H2, H3, H4: MountingHole; MountingHole_3.2mm_M3
J1, J2, J3, J4, J5: 250-1404; CONN_250-1404_WAG
J6: GND 12V DC +; CONN_2604-1102_4_WAG
J7: DCC IN; CONN_2604-1102_4_WAG
J8: I²C D C + -; Pin_Header_Straight_1x04_Pitch2.54mm
J22, J23: CAN-BUS; A20042LPFS
JP1: DCC B; Pin_Header_Straight_1x02_Pitch2.54mm
JP2: DCC CAN; Pin_Header_Straight_1x02_Pitch2.54mm
JP3: CAN-Term; Pin_Header_Straight_1x02_Pitch2.54mm
JP4: 12V CAN; Pin_Header_Straight_1x02_Pitch2.54mm
JP5: Prog1; Pin_Header_Straight_1x02_Pitch2.54mm
JP6: Prog2; Pin_Header_Straight_1x02_Pitch2.54mm
JP7: COM; Pin_Header_Straight_1x02_Pitch2.54mm
JP8: Shield; Pin_Header_Straight_1x02_Pitch2.54mm
R1: 1k5; R_Axial_DIN0207_L6.3mm_D2.5mm_P7.62mm_Horizontal
R2, R6: 10K; R_Axial_DIN0207_L6.3mm_D2.5mm_P7.62mm_Horizontal
R4: 4,7k; R_Axial_DIN0207_L6.3mm_D2.5mm_P7.62mm_Horizontal
R5: 22k; R_Axial_DIN0207_L6.3mm_D2.5mm_P7.62mm_Horizontal
R7, R8: 4k7; R_Axial_DIN0207_L6.3mm_D2.5mm_P7.62mm_Horizontal
R9, R10: 1k; R_Array_SIP6
R20: 470; R_Axial_DIN0207_L6.3mm_D2.5mm_P7.62mm_Horizontal
Shield1: CAN-BUS-MODULE; MCP2515_CAN_MODULE
U1: 6N136; DIP-8_W7.62mm
U2: Arduino_Nano
U3, U4: ULN2803A; DIP-18_W7.62mm
U5: TSR_1-2450; DCDC-Conv_TRACO_TSR-1

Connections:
+5V: C1.1, J8.2, R2.1, R6.1, R7.2, R8.2, R20.2, Shield1.1 (VCC), U1.8, U2.27 (+5V), U5.3 (Vout)
+12V: D2.2 (A), J1.3, J2.3, J3.3, J4.3, J5.3, J6.1, J6.2, JP7.2
GND: C1.2, D4.1 (K), J1.1, J2.1, J3.1, J4.1, J5.1, J6.3, J6.4, J8.1, J22.3, J22.7, J23.3, J23.7, JP5.2 (B), JP6.2 (B), JP8.2, R9.1 (common), R10.1 (common), Shield1.2 (GND), U1.5, U2.29 (GND), U3.9 (GND), U4.9 (GND), U5.2 (GND)
unnamed: D1.1 (K), R1.1, U1.2
unnamed: D1.2 (A), J7.1, J7.2, JP1.1 (A), U1.3
unnamed: D2.1 (K), D3.1 (K), U5.1 (Vin)
unnamed: D3.2 (A), JP4.2
unnamed: D4.2 (A), R20.1
unnamed: DS1.1 (A_1), U2.7 (D4), U4.4 (I4)
unnamed: DS1.2 (A_2), U2.8 (D5), U4.3 (I3)
unnamed: DS1.3 (A_3), U2.9 (D6), U4.2 (I2)
unnamed: DS1.4 (A_4), U2.10 (D7), U4.1 (I1)
unnamed: DS1.5 (A_5), U2.11 (D8), U3.6 (I6)
unnamed: DS1.6 (A_6), U2.12 (D9), U3.5 (I5)
unnamed: DS1.7 (A_7), U2.20 (A1), U3.4 (I4)
unnamed: DS1.8 (A_8), U2.19 (A0), U3.3 (I3)
unnamed: DS1.9 (A_9), U2.21 (A2), U3.2 (I2)
unnamed: DS1.10 (A_10), U2.22 (A3), U3.1 (I1)
unnamed: DS1.11 (K_1), R10.2 (R1)
unnamed: DS1.12 (K_2), R10.3 (R2)
unnamed: DS1.13 (K_3), R10.4 (R3)
unnamed: DS1.14 (K_4), R10.5 (R4)
unnamed: DS1.15 (K_5), R10.6 (R5)
unnamed: DS1.16 (K_6), R9.6 (R5)
unnamed: DS1.17 (K_7), R9.5 (R4)
unnamed: DS1.18 (K_8), R9.4 (R3)
unnamed: DS1.19 (K_9), R9.3 (R2)
unnamed: DS1.20 (K_10), R9.2 (R1)
unnamed: J1.2, U3.17 (O2)
unnamed: J1.4, U3.18 (O1)
unnamed: J2.2, U3.15 (O4)
unnamed: J2.4, U3.16 (O3)
unnamed: J3.2, U3.13 (O6)
unnamed: J3.4, U3.14 (O5)
unnamed: J4.2, U4.17 (O2)
unnamed: J4.4, U4.18 (O1)
unnamed: J5.2, U4.15 (O4)
unnamed: J5.4, U4.16 (O3)
unnamed: J7.3, J7.4, JP2.1 (A), R1.2
unnamed: J8.3, R7.1, U2.24 (A5)
unnamed: J8.4, R8.1, U2.23 (A4)
unnamed: J22.1, J23.1, Shield1.H (CANH)
unnamed: J22.2, J23.2, Shield1.L (CANL)
unnamed: J22.4, J23.4, JP2.2 (B)
unnamed: J22.5, J23.5, JP1.2 (B)
unnamed: J22.6, J23.6
unnamed: J22.8, J23.8, JP4.1
unnamed: J22.MH3, J22.MH4, J23.MH3, J23.MH4, JP8.1
unnamed: JP3.1, Shield1.1.1 (J1-1)
unnamed: JP3.2, Shield1.1.2 (J1-2)
unnamed: JP5.1 (A), R4.2
unnamed: JP6.1 (A), R5.2
unnamed: JP7.1, U3.10 (COM), U4.10 (COM)
unnamed: R2.2, U1.6, U2.5 (D2)
unnamed: R4.1, R5.1, R6.2, U2.25 (A6)
unnamed: Shield1.3 (CS), U2.13 (D10)
unnamed: Shield1.4 (MISO), U2.15 (D12)
unnamed: Shield1.5 (MOSI), U2.14 (D11)
unnamed: Shield1.6 (SCK), U2.16 (D13)
unnamed: Shield1.7 (INT), U2.6 (D3)

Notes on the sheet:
DCC-Interface
B A


Board: 2 copper layers, 109.2 x 81.3 mm, 44 parts (1 on the bottom side), 60 nets.

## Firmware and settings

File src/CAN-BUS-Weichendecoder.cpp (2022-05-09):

#include <Arduino.h>
#include <EEPROM.h>

#include "CanCommunicator.h"
#include "CanConfiguration.h"
#include "ConfigPin.h"
#include "Debug.h"
#include "I2C_Tools.h"
#include "SerialConfiguration.h"
#include "Signal.h"
#include "Weiche.h"

#define IMPULSE_LENGTH 2000

ConfigPin configPin;
CAN_CONFIGURATION can_configuration;
I2C_Tools i2c;

#define LED_1 4
#define LED_2 5
#define LED_3 6
#define LED_4 7
#define LED_5 8
#define LED_6 9
#define LED_7 A1
#define LED_8 A0
#define LED_9 A2
#define LED_10 A3

OUTPUT_CONF configuration = {
    OUTPUT_CONTROL::OUTPUT_MODE::IMPULSE,
    OUTPUT_CONTROL::ACTIVE_MODE::high,
    IMPULSE_LENGTH,
    IMPULSE_LENGTH};

/** Callback-Funktionen */
void change(uint16_t address);
void changeWeiche(uint16_t address);
void changeSignal(uint16_t address);

OutputControl *control = (OutputControl *)malloc(sizeof(OutputControl) * 10);
// Weiche *weiche = (Weiche *)malloc(sizeof(Weiche) * 5);
// Signal *signal = (Signal *)malloc(sizeof(Signal) * 6);

Weiche weiche[5];
Signal signal[6];

SerialConfiguration serialConfiguration = SerialConfiguration(*changeWeiche, *changeSignal);
CanComm canComm = CanComm(&can_configuration, weiche, signal, *change);

#include "Dcc.h"

void changeWeiche(uint16_t address) {
  for (byte i = 0; i < 5; i++) {
    if (weiche[i].find(address)) {
      Serial.print(F("DEBUG Address Weiche["));
      Serial.print(address);
      Serial.println(F("] gefunden"));

      weiche[i].change(address);
    }
  }
}

void changeSignal(uint16_t address) {
  for (byte i = 0; i < 6; i++) {
    if (signal[i].find(address)) {
      Serial.print(F("DEBUG: Address Signal ["));
      Serial.print(address);
      Serial.println(F("] found"));

      signal[i].change(address);
    }
  }
}

void change(uint16_t address) {
  changeWeiche(address);
  changeSignal(address);
}

void initDccConfiguraion(byte configPin, byte canModulId) {
  Serial.print(F("DCC-Address: ["));
  uint16_t dccAddr = Dcc.getCV(CV_ACCESSORY_DECODER_ADDRESS_LSB) + (8 * Dcc.getCV(CV_ACCESSORY_DECODER_ADDRESS_MSB));
  Serial.print(dccAddr);
  Serial.println(F("]"));

  Serial.print(F("Config Pin: ["));
  Serial.print(configPin);
  Serial.println(F("]"));

  if (configPin == 1) {
    uint16_t newDccAddr = ((canModulId - 1) * 5) + 1;

    Serial.print(F("Neue DCC-Addresse: ["));
    Serial.print(newDccAddr);
    Serial.println(F("]"));

    Dcc.setCV(CV_ACCESSORY_DECODER_ADDRESS_LSB, newDccAddr & 0xFF);
    Dcc.setCV(CV_ACCESSORY_DECODER_ADDRESS_MSB, newDccAddr >> 8);
  }
}

void initSignal() {
  I2CSignal i2csignal;
  i2csignal.init_pcf8574();

  for (uint8_t i = 0; i < 5; i++) {
    signal[i] = Signal(can_configuration.config.firstIdSignal + (i * 4), 51 + (i * 2), i, &i2csignal, SIGNAL::SOCKET::PIN);
  }
  for (uint8_t i = 5; i < 6; i++) {
    signal[i] = Signal(can_configuration.config.firstIdSignal + (i * 4), 51 + (i * 2), i, &i2csignal, SIGNAL::SOCKET::RJ12);
  }
}

void initWeiche() {
  Serial.println(F("Init Weiche Beginn"));

  control[0] = OutputControl(&configuration, LED_1);
  control[1] = OutputControl(&configuration, LED_2);
  control[2] = OutputControl(&configuration, LED_3);
  control[3] = OutputControl(&configuration, LED_4);
  control[4] = OutputControl(&configuration, LED_5);
  control[5] = OutputControl(&configuration, LED_6);
  control[6] = OutputControl(&configuration, LED_7);
  control[7] = OutputControl(&configuration, LED_8);
  control[8] = OutputControl(&configuration, LED_9);
  control[9] = OutputControl(&configuration, LED_10);

  for (uint8_t i = 0; i < 5; i++) {
    weiche[i] = Weiche(control[i * 2], control[(i * 2) + 1], can_configuration.config.firstIdWeiche + i * 2, 41 + i);
  }
  Serial.println(F("Init Weiche End"));
}

void setup() {
  Serial.begin(115200);

  free_dump();

  byte value = configPin.readCongigPin();
  Serial.print(F("Wert ConfigPin: ["));
  Serial.print(value);
  Serial.println(F("]"));

  Serial.println(F("> init i2c ..."));
  i2c.init_i2c();
  Serial.println(F("= done"));

  Serial.println(F("> scan i2c ..."));
  i2c.scan_i2c();
  Serial.println(F("= done"));

  canComm.initCanConfiguraion(value);

  serialConfiguration.init(can_configuration, Dcc);

  serialConfiguration.printConfiguration();

  initWeiche();
  initSignal();

  free_dump();

  canComm.init();

  free_dump();

  init_DCC();
  initDccConfiguraion(value, can_configuration.config.modulId);
}

void processWeiche() {
  for (byte k = 0; k < 5; k++) {
    weiche[k].process();
  }
}

void processSignal() {
  for (byte k = 0; k < 6; k++) {
    signal[k].process();
  }
}

void loop() {
  serialConfiguration.process();
  canComm.processCanMessage();
  processWeiche();
  processSignal();
  Dcc.process();
  dccWriteFactotyDefaults();

  delay(5);
}

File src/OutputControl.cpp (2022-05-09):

#include "OutputControl.h"

OutputControl::OutputControl() {}

OutputControl::OutputControl(OUTPUT_CONF *_configuration, byte _pin) {
  this->configuration = _configuration;
  this->pin = _pin;

  // Ausgange "ausschalten" und state u. lastChange setzen
  switch (this->configuration->activeMode) {
    case OUTPUT_CONTROL::ACTIVE_MODE::low:
      pinMode(pin, INPUT_PULLUP);
      state = HIGH;
      break;
    case OUTPUT_CONTROL::ACTIVE_MODE::high:
      pinMode(pin, INPUT);
      state = LOW;
      break;
  }
  pinMode(pin, OUTPUT);
  lastChanged = millis();

  // Pause zwischen den Implsen definieren
  if (this->configuration->outputMode == OUTPUT_CONTROL::OUTPUT_MODE::IMPULSE) {
    this->configuration->duration_2 = this->configuration->duration;
  } else {
    this->configuration->duration_2 = 0;
  }
}

void OutputControl::writeState() {
  Serial.print(F("DEBUG OC "));
  Serial.print(F("Pin: "));
  Serial.print(pin);
  Serial.print(F(" State ["));
  Serial.print(state);
  Serial.println(F("]"));
  digitalWrite(pin, state);
}

boolean OutputControl::isImpulePosible() {
  Serial.print(lastChanged / 1000);
  Serial.print("-");
  Serial.print(this->configuration->duration / 1000);
  Serial.print("-");
  Serial.print(this->configuration->duration_2 / 1000);
  Serial.print("-");
  Serial.println(millis() / 1000);
  if (lastChanged == 0) {
    return true;
  }
  if (isOn()) {  // Bei Impulse ist der Ausgang aktiv
    return false;
  }
  if (lastChanged + this->configuration->duration + this->configuration->duration_2 > millis()) {
    // Serial.println("Noch nicht wieder frei");
    return false;
  }
  return true;
}

void OutputControl::on() {
  // Serial.println("on");
  if (this->configuration->outputMode != OUTPUT_CONTROL::OUTPUT_MODE::PERMANENT) {
    // return;
  }

  // Serial.print("active Mode: [");
  // Serial.print(this->actor->activeMode);
  // Serial.println("]");
  if (state == this->configuration->activeMode) {
    // Serial.println("Keine Änderung");
    return;
  }

  state = this->configuration->activeMode;
  lastChanged = millis();
  this->writeState();
}

void OutputControl::off() {
  // Serial.println("off");
  if (this->configuration->outputMode == OUTPUT_CONTROL::OUTPUT_MODE::PERMANENT) {
    // return;
  }

  // Serial.print("active Mode: [");
  // Serial.print(this->actor->activeMode);
  // Serial.println("]");
  if (state != this->configuration->activeMode) {
    return;
  }

  state = (!this->configuration->activeMode);
  if (this->configuration->outputMode != OUTPUT_CONTROL::OUTPUT_MODE::IMPULSE) {
    lastChanged = millis();
  }
  this->writeState();
}

void OutputControl::toggle() {
  if (state == this->configuration->activeMode) {
    this->off();
  } else {
    this->on();
  }
}

void OutputControl::impulse() {
  // Serial.print("impulse: Mode: [");
  // Serial.print(this->actor->outputMode);
  // Serial.println("]");
  if (this->configuration->outputMode == OUTPUT_CONTROL::OUTPUT_MODE::IMPULSE) {
    this->on();
  }
}

boolean OutputControl::isOn() {
  boolean result = (state == this->configuration->activeMode);
  return result;
}

void OutputControl::offFlash() {
  if (this->configuration->outputMode == OUTPUT_CONTROL::OUTPUT_MODE::FLASH_ON) {
    this->configuration->outputMode = OUTPUT_CONTROL::OUTPUT_MODE::FLASH_OFF;
  }
}

void OutputControl::onFlash() {
  if (this->configuration->outputMode == OUTPUT_CONTROL::OUTPUT_MODE::FLASH_OFF) {
    this->configuration->outputMode = OUTPUT_CONTROL::OUTPUT_MODE::FLASH_ON;
  }
}

void OutputControl::process() {
  if (this->configuration->outputMode == OUTPUT_CONTROL::OUTPUT_MODE::FLASH_ON) {
    this->flash();
  }

  if (this->configuration->outputMode == OUTPUT_CONTROL::OUTPUT_MODE::FLASH_OFF) {
    if (isOn()) {
      this->flash();
    }
  }

  if (this->configuration->outputMode == OUTPUT_CONTROL::OUTPUT_MODE::IMPULSE) {
    if (isOn()) {
      this->flash();
    }
  }
}

void OutputControl::flash() {
  // Serial.print(this->actor->lastChanged);
  // Serial.print(" + ");
  // Serial.print(this->actor->duration);
  // Serial.print(" > ");
  // Serial.println(millis());

  if (lastChanged + this->configuration->duration > millis()) {
    // Serial.println("Kein Umschalten");
    return;
  }

  // Serial.println("Umschalten");

  this->toggle();
}

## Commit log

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2021-03-22 Schaltplan angepasst
    [CAN-BUS.kicad_pcb, CAN-BUS.sch]
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2021-03-22 Schaltung erweitert
    [CAN-BUS-Weichendecoder.fzz]
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2021-04-18 Dateien umbenannt
    [Weichensimulator-links.kicad_pcb, Weichensimulator-links.sch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]
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2021-04-22 weitere Weichensimulator-Bauteile hinzugefügt
    [Weichensimulator-45links.kicad_pcb, Weichensimulator-45links.sch, Weichensimulator-45rechts.kicad_pcb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]
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2021-04-23 Platine für Adapter 2x3 zu 1x6 hinzugefügt
    [2x3zu1x6.kicad_pcb, 2x3zu1x6.sch]
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2021-05-04 Ecken rund gemacht, alle mit Montagelöcher
    [2x3zu1x6.kicad_pcb, Signalsimulator.kicad_pcb, Signalsimulator.sch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]
2021-05-06 Platinen, die an jlcpcb geschickt worden sind.
    [2x3zu1x6-B_Cu.gbl, 2x3zu1x6-B_Mask.gbs, 2x3zu1x6-B_Paste.gbp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]
2021-05-06 Aktueller Stand
    [CAN-BUS-Weichendecoder.kicad_pcb, CAN-BUS-Weichendecoder.sch]
2021-05-06 Dateien gelöscht/umbeannt
    [Signalsimulator-B_Cu.gbl, Signalsimulator-B_Mask.gbs, Signalsimulator-B_Paste.gbp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]
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2021-05-21 v2.0 hinzugefügt
    [Weichensimulator-rechts-B_Cu.gbl, Weichensimulator-rechts-B_Mask.gbs, Weichensimulator-rechts-B_Paste.gbp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]
2021-05-21 2. Umschalter herausgeführt
    [Weichensimulator-rechts.kicad_pcb, Weichensimulator-rechts.sch]
2021-06-29 Version 2, jetzt korrekt und auch nutzbar für links, 2. Umschalter herausgeführt
    [Weichensimulator-rechts.kicad_pcb, Weichensimulator-rechts.sch]
2021-06-29 Bezeichung auf der Bestückungsseite
    [Weichensimulator-45links.kicad_pcb, Weichensimulator-45links.sch]
2021-06-29 Bezeichnung nun auf der Besrückungsseite
    [Weichensimulator-45rechts.kicad_pcb, Weichensimulator-45rechts.sch]
2021-06-29 beschreibung auf Bestückungssete, 90°-Kurven durch 45° erstetzt
    [Weichensimulator-links.kicad_pcb, Weichensimulator-links.sch]
2021-06-29 Werte der Widerstände hinzugefügt
    [Signalsimulator.sch]
2021-06-29 Platine weiterentwickelt, aktueller Arbeitsstand
    [CAN-BUS-Weichendecoder.kicad_pcb, CAN-BUS-Weichendecoder.sch]
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2021-10-01 Auch die Bedruckung jetzt auf beiden Seiten, Platine jetzt komplett für Links und Rechts
    [CAN-BUS-Weichendecoder.kicad_pcb, CAN-BUS-Weichendecoder.sch, Weichensimulator-rechts.kicad_pcb]
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2021-10-05 Wago-Klemmen 250-140x verwendet
    [CAN-BUS-Weichendecoder.kicad_pcb, CAN-BUS-Weichendecoder.sch]
2021-10-06 PCP weiterentwickelt
    [CAN-BUS-Weichendecoder.kicad_pcb, CAN-BUS-Weichendecoder.sch]
2021-10-06 Beschriftung für A und G korrigiert, Bauteil-Betruckung auf beiden Seiten
    [Weichensimulator-rechts.kicad_pcb, Weichensimulator-rechts.sch]
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2021-10-09 Erster kompletter Entwurf der Platine
    [CAN-BUS-Weichendecoder.kicad_pcb, CAN-BUS-Weichendecoder.sch]
2021-10-10 +5 analog zu GND verlegt
    [CAN-BUS-Weichendecoder.kicad_pcb]
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2021-10-19 Aufgeteilt auf zwei Platinen
    [Belegmelder_Neustadt.kicad_pcb, Belegmelder_Neustadt.sch, CAN-BUS-Weichendecoder-Signal.kicad_pcb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]
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2021-10-27 Aktuellen zwischenstand gesichert
    [CAN-BUS-Weichendecoder-Weiche-small.fzz, CAN-BUS-Weichendecoder-Weiche-small.kicad_pcb, CAN-BUS-Weichendecoder-Weiche-small.sch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]
2021-10-28 Buchen und Stecker vertauscht und Anordnung kompakter
    [CAN-BUS-Weichendecoder-Weiche.kicad_pcb, CAN-BUS-Weichendecoder-Weiche.sch]
2021-11-05 Anordnung der Bauteile kompakter, 2 statt 3 prog-Pins, nur eine Verbindung zur Weiche
    [CAN-BUS-Weichendecoder-Weiche.kicad_pcb, CAN-BUS-Weichendecoder-Weiche.sch]
2021-11-06 CAN-Bus-Belegun geändert
    [CAN-BUS-Weichendecoder-Weiche.kicad_pcb, CAN-BUS-Weichendecoder-Weiche.sch]
2021-11-17 Buchen zu den Weichen gedreht, damit sie besser auf das Board passsen
    [CAN-BUS-Weichendecoder-Weiche.kicad_pcb, CAN-BUS-Weichendecoder-Weiche.sch]
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2022-01-01 Aufgeräumt
    [Belegmelder_Neustadt.kicad_pcb, Belegmelder_Neustadt.kicad_sch, Belegmelder_Neustadt.sch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]
2022-01-01 Alte Dateien entfernt
    [Signalsimulator.sch]
2022-01-01 Alte Datei gelöscht, 6er-Dateien hinzugefügt
    [2x3zu1x6-B_Cu.gbl, 2x3zu1x6-B_Mask.gbs, 2x3zu1x6-B_Paste.gbp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]
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2022-02-19 Ausgänge in zwei Blöcke aufgetreilt, Ausgangsspannung kann extern eingespeist werden
    [CAN-BUS-Weichendecoder-Signal.kicad_pcb, CAN-BUS-Weichendecoder-Signal.kicad_sch]
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2022-02-20 Beschriftung bearbeit und Bemaßung erweitert
    [CAN-BUS-Weichendecoder-Signal.kicad_pcb]
2022-02-20 Flächen gefült und DRC-Warnung beseitigt
    [Signalsimulator.kicad_pcb]
2022-02-21 Lage der Stecker angepasst
    [CAN-BUS-Weichendecoder-Signal.kicad_pcb]
2022-02-21 i2c-Adresse bewchriftet, RJ12 neu ausgerichtet
    [CAN-BUS-Weichendecoder-Signal.kicad_pcb]
2022-02-21 Version auf 1.1 geändert + Kosmetik
    [CAN-BUS-Weichendecoder-Signal.kicad_pcb]
2022-04-01 Belegmelder verschoben in ein eignes Projekt
    [Belegmelder_Neustadt.kicad_pcb, Belegmelder_Neustadt.kicad_sch, Belegmelder_Neustadt.sch]
2022-04-01 Widerständer auf Rückseite, Widerstandswerte angepasst
    [Signalsimulator.kicad_pcb, Signalsimulator.kicad_sch]
2022-04-01 Pullup-Widerstand hinzugefügt; Power-LED hinzugefügt
    [CAN-BUS-Weichendecoder-Signal.kicad_pcb, CAN-BUS-Weichendecoder-Signal.kicad_sch]
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2023-11-30 Kicad-Dateien in Wurzel verschoben
    [2x3zu1x6.kicad_pcb, 2x3zu1x6.kicad_sch, CAN-BUS-Weichendecoder-Signal.kicad_pcb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]

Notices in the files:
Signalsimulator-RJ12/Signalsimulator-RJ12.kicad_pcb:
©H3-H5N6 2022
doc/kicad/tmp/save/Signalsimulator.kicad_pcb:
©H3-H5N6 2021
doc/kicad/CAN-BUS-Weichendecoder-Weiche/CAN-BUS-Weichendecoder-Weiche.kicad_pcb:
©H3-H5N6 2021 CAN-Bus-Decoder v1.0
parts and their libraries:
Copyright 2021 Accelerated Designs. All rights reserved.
